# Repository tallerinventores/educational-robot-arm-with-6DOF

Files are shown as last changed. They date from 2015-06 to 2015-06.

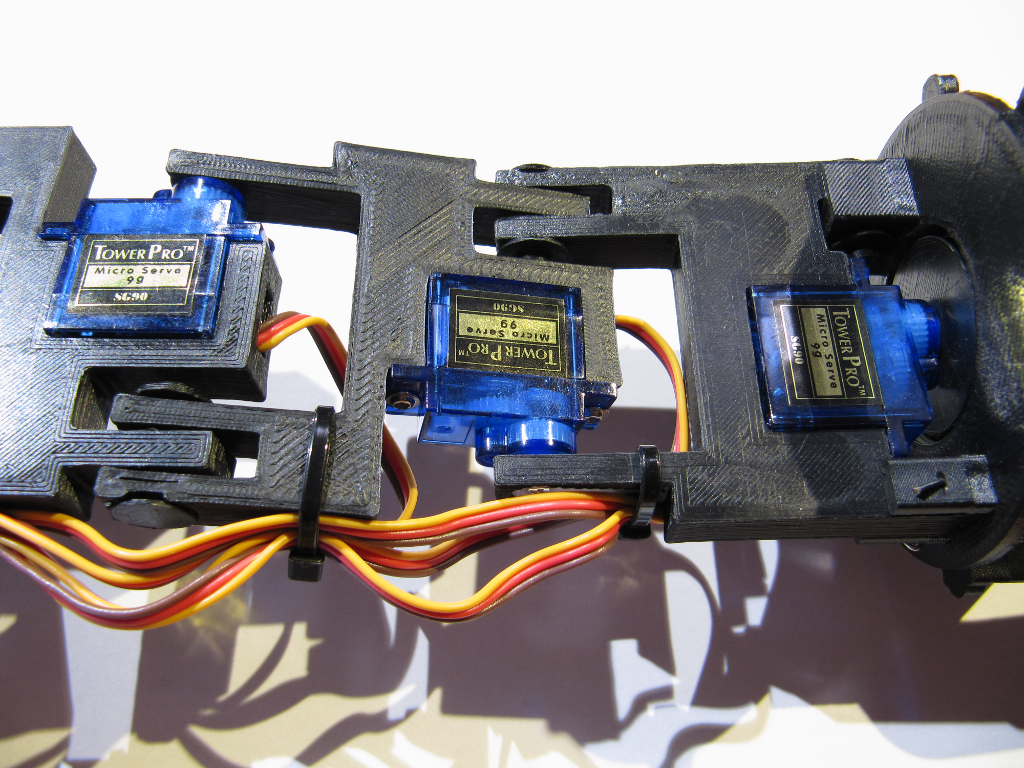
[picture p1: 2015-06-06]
img/photo-era6dof-4.png

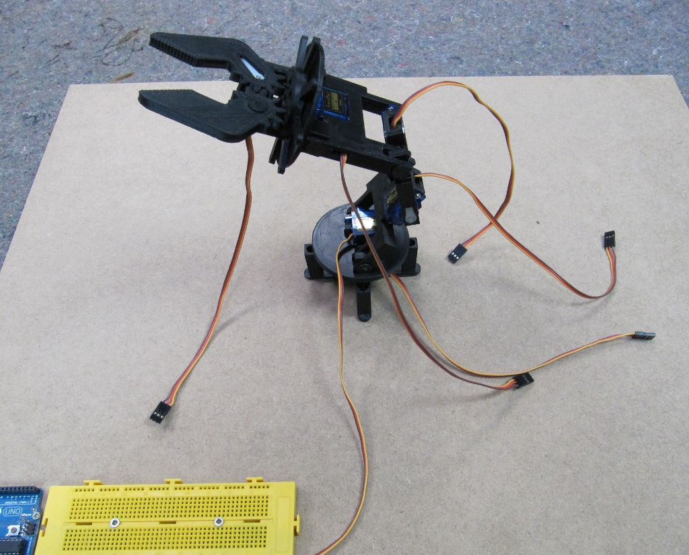
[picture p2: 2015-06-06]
img/photo-era6dof-1.png

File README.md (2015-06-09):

# Educational Robot Arm with 6DOF #

> Robot arm w/ 6DOF for educational use

* * *

## Resumen ##

Brazo robótico con seis grados de libertad para uso en entornos educativos. El
brazo ha sido desarrollado y optimizado para impresión 3D y pensando en su bajo
coste y facilidad de montaje y uso. Es personalizable al poder aumentar o
disminuir los grados de libertad, del mismo modo que permite controlarse desde
diferentes plataformas.

## Instalación ##

En esta sección se cubre la instalación de software y hardware para el montaje
recomendado, mediante [Scratch](https://scratch.mit.edu/) y
[Arduino](http://www.arduino.cc/).

### Requerimientos de software ###

Para poder usar Scratch (v2.0 online) con Arduino, es necesario
[s2a_fm](https://github.com/MrYsLab/s2a_fm) una extensión de Scratch para
comunicarse con Arduino. Para generar los archivos aptos para la impresora 3D
desde los archivos `.stl` será necesario adicionalmente un software para esta
función, como puede ser [Slic3r](http://slic3r.org/).

Ver los requerimientos de mencionados programas previamente.

### Requerimientos de hardware ###

Será necesario para su montaje y uso una fuente de alimentación que proporcione
7.5W a 5V, un Arduino Uno o equivalente, seis servomotores tipo 9g con sus
correspondientes accesorios (tornillos y cuernos). El brazo está optimizado para
usar los servos **TowerPro SG90**.

## Uso ##

Instrucciones de montaje y puesta en marcha.

### Montaje del brazo robótico ###

1.  Imprimir una unidad de los archivos `feet.stl`, `grip.stl`, `plate.stl`,
    `wrist`, `rest.stl`, `axle.stl`, `left_jaw.stl` and `right_jaw.stl`.
    Imprimir dos unidades de `arm.stl`. Imprimir cinco unidades de
    `fastener.stl` y `clip.stl`. Puede ser necesario repasar las piezas impresas
    con el fin de eliminar rebabas.  
2.  Presentar la base del brazo (_feet_) en un tablero y atornillarlo al mismo
    con cuatro tornillos para madera.  
3.  Colocar un servo (sin cuerno) en la base, haciéndo coincidir el eje del
    mismo con el centro de la base y atornillarlo a la misma con los tornillos
    de montaje del servo.  
4.  Poner el cuerno del servo sobre la huella con su forma en la parte inferior
    del plato (_grip_), considerando que el eje estará en hacia abajo.  
5.  Insertar el plato (_plate_) en la pieza anterior, asegurando que el cuerno
    encaja en su posición.  
6.  Comprobar que una vez colocado el conjunto del plato sobre el servo, éste
    realiza el giro de la forma deseada. En ese momento se puede atornillar el
    servo al cuerno con el tornillo provisto por el servo.  
7.  Fijar el siguiente servo con dos tornillos en la parte superior del plato,
    de forma que quede el eje centrado con respecto al plato.  
8.  Del primer tramo del brazo (_arm_), hacer coincidir el orificio destinado
    para el cuerno del servo en el eje del mismo mientras que se inserta el otro
    extremo en el saliente del plato.  
9.  Asegurar el brazo en esta posición usando un pasador (_fastener_ y _clip_),
    insertando el primero desde fuera hacia dentro, y retenerlo aquí con el
    segundo.  
10. Encastrar el cuerno en el brazo y asegurar que el servo es capaz de realizar
    giro completo de un extremo al otro. Entonces atornillarlo al servo.  
11. Atornillar un servo en el extremo del tramo del brazo recién montado, con el
    eje lo más distante a la base.  
12. Repetir los pasos ocho al once para el siguiente tramos de brazo (_arm_),
    estándo este montado rotado con respecto al anterior.   
13. De la misma manera, poner el último tramo (_wrist_) en la parte superior del
    brazo, también rotado con respecto al tramo intermedio.  
14. Introducir el servo del último tramo de forma que el eje del mismo quede
    centrado y atornillarlo.  
15. Hacer coincidir los dos orificios del último tramo montado con los
    respectivos del asiento (_rest_) y fijarlos. El grande mediante pasador como
    anteriormente y el pequeño con un alambre y doblándolo después. Un clip para
    papel es perfecto para esta función. Cortar el sobrante una vez doblado en
    los extremos.  
16. Encajar las dos piezas que permitirán que rote la pinza (_gripper_ y
    _axle_). Insertar el cuerno del servo en la endidura central de los mismos.  
17. Presentar este bloque contra el asiento y asegurar que gira de la forma
    deseada antes de atornillar el cuerno al servo.  
18. Montar el último servo en la parte más alta del brazo, con el eje hacia el
    centro. Atornillarlo por la parte externa.  
19. Con el cuerno del servo dentro de la mitad derecha de la pinza
    (_right\_jaw_), insertarlo en el eje del servo correspondiente y asegurar
    que realiza el giro necesario. Acto seguido atornillarlo.  
20. Colocar la otra mitad de pinza (_left\_jaw_), engranarla con la primera de
    forma que realicen el cierre en el centro. Fijarlo al cuerpo del brazo con
    un pasador.   
21. Realizar una correcta gestión de cableado para asegurar que todos llegan
    hasta la base sin impedir el movimiento de cada tramo, ni que son aplastado
    por los mismos. Puede ser necesario extender algunos de ellos.

### Conexión eléctrica ###

Todas las alimentaciones de los servomotores van en paralelo y a la fuente de
alimentación. Las señales de control de los servos van a Arduino, usando las
conexiones del dos al siete para los servos de la pinza a la base,
respectivamente y por orden. La masa del Arduino y de la fuente de alimentación
ha de ser compartida. Conectar el Arduino a un puerto USB libre del ordenador a
usar.

### Firmware ###

El Arduino deberá tener cargado el firmware Firmata (incluido con Arduino IDE
bajo en nombre de `StandardFirmata`).

### Software ###

Con el Arduino conectado al ordenador, lanzar s2a_fm con el nombre del puerto
donde realizar la comunicación con Arduino. Por ejemplo:

        python s2a_fm.py /dev/ttyACM0

Abrir Scratch y cargar el proyecto `educational-robot-arm-with-6DOF.sb2`, una
vez hecho, se podrá ver en la interfaz gráfica los posibles movimientos del
brazo en forma de flechas para dichas órdenes. Se presentan dos formas de mover
el brazo:

-   Semiautomática.  
-   Manual.

Para conmutar entre ellos se usa el botón situado en la esquina superior
derecha, que al ser pulsado mostrará las opciones **STEP**, **BIG STEP**,
**FULL** y **MANUAL**. Las tres primeras son semiautomáticas, mientras que la
última permite controlar el brazo robótico manualmente.

En semiautomático, es tan sencillo como pulsar la flecha correspondiente al
tramo y dirección deseado para realizar un movimiento angular de tantos grados
como esté seleccionado.

En manual, ha de seleccionarse el tramo a mover, después seleccionar el número
de grados a mover dicho tramo y deseleccionar el tramo para efectuar el
movimiento.

La interfaz gráfica incluye los límites físicos del brazo para prevenir la
rotación de los servos más allá de estos.

### Bugs ###

Se han observado los siguientes problemas:

-   Las dos partes de la pinza tienen cierta holgura, eso provoca que no se
    cierren alineadas.  
-   El brazo totalmente extendido en horizontal presenta demasiada carga para
    los servos más cercanos a la base.  
-   El software de control provoca al inicio movimientos extraños.  
-   En determinados momentos hay servos que se deshabilitan sin razón aparente.
    (Problema de PyMata?).  
-   Por protocolo de Firmata, es necesario un pequeño tiempo entre órdenes para
    asegurar que son recibidas y procesadas. (Implementado).

## Enlaces externos ##

Este proyecto también está presente en:

-   [Scratch](https://scratch.mit.edu/projects/65804696/).  
-   [Thingiverse](http://www.thingiverse.com/thing:436096).

## Créditos ##

Proyecto realizado por Taller de Inventores 2015, representado por:

-   kwendenarmo <kwendenarmo@akornsys-rdi.net>

Alumnos de Centro de Formación Padre Piquer:

-   G, Ayman El-  
-   S, Safaa

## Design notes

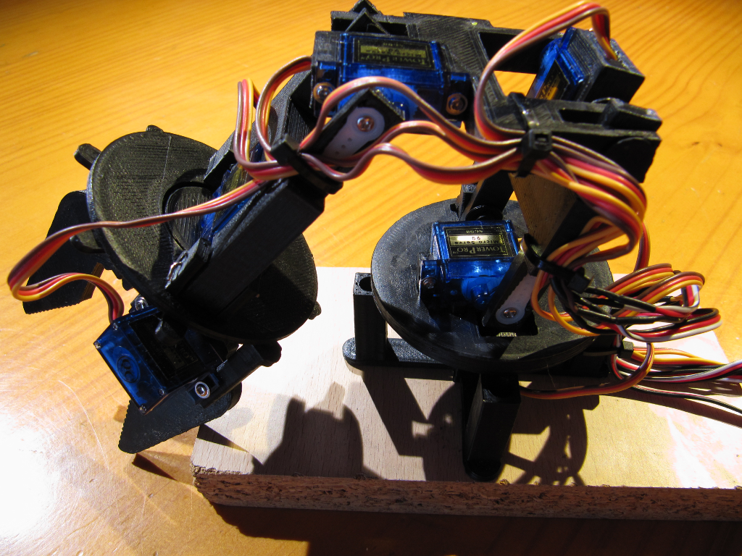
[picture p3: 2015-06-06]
img/photo-era6dof-2.png

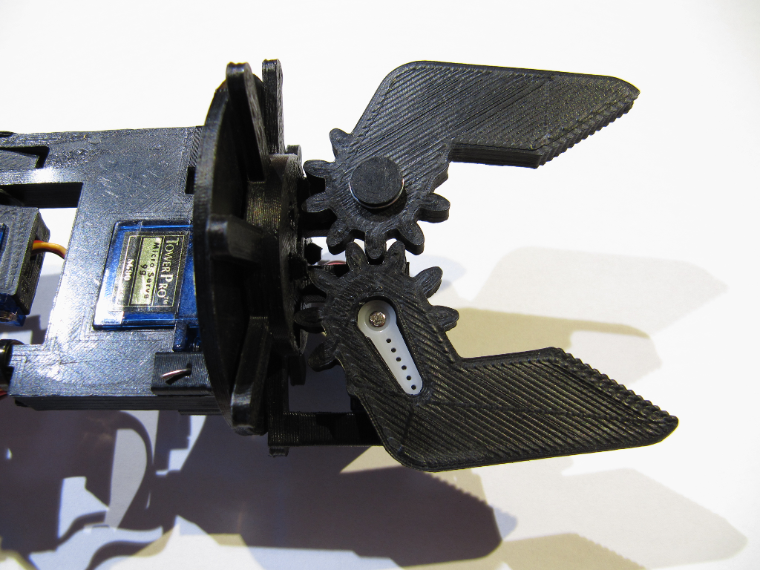
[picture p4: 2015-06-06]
img/photo-era6dof-5.png

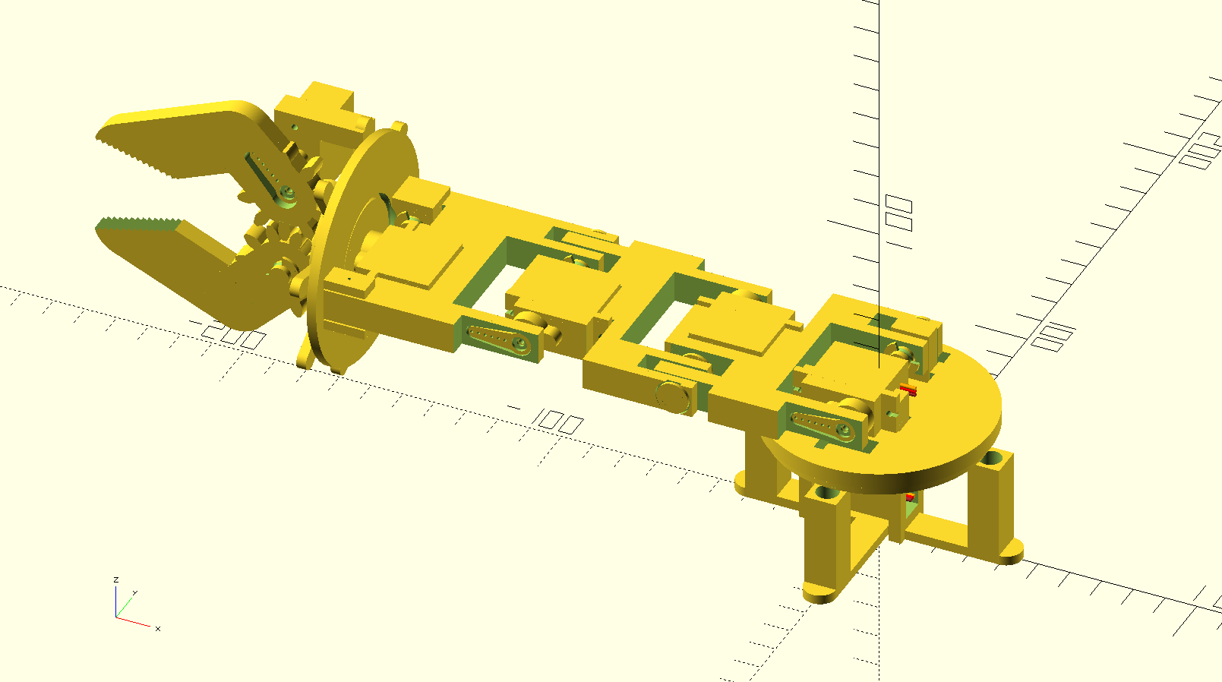
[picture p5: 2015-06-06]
img/render.png

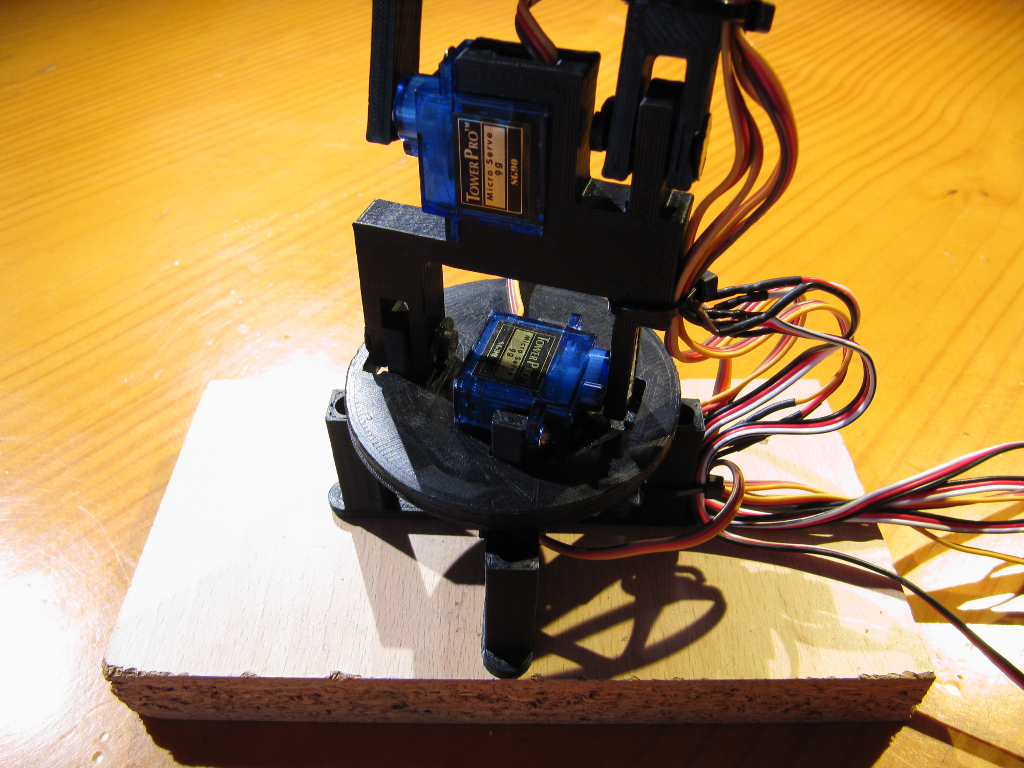
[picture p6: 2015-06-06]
img/photo-era6dof-3.png

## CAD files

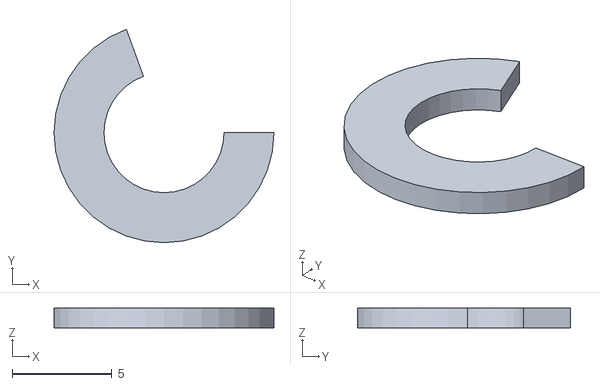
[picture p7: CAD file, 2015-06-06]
3d/clip.stl
11.0 x 10.7 x 1.00

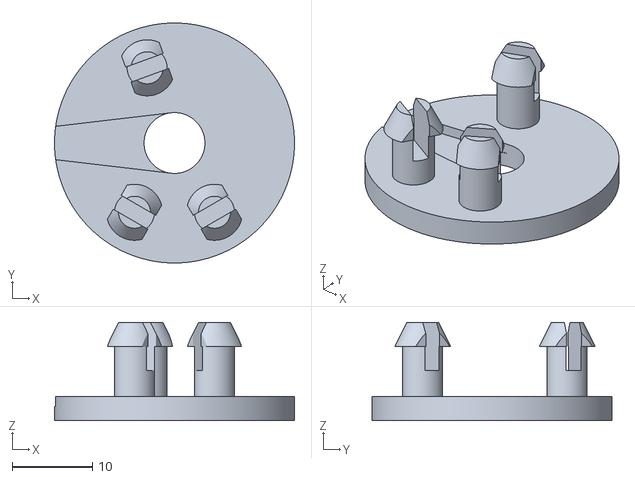
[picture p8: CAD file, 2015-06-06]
3d/axle.stl
30.0 x 30.0 x 12.2

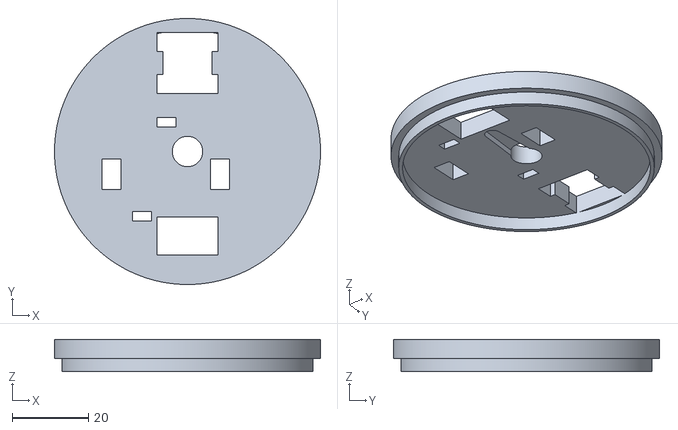
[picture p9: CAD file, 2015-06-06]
3d/plate.stl
70.0 x 70.0 x 8.50

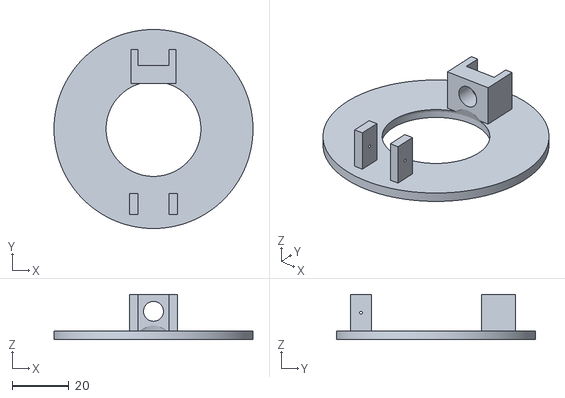
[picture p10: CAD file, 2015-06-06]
3d/rest.stl
70.0 x 70.0 x 16.0

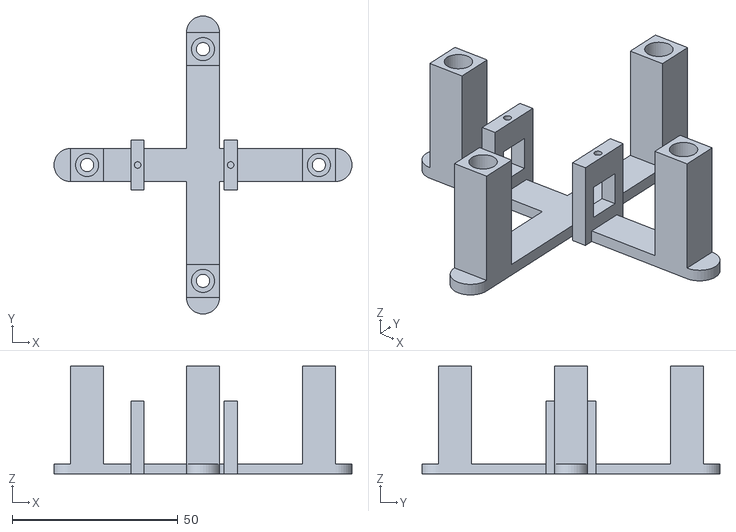
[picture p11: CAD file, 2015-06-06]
3d/feet.stl
90.0 x 90.0 x 32.5

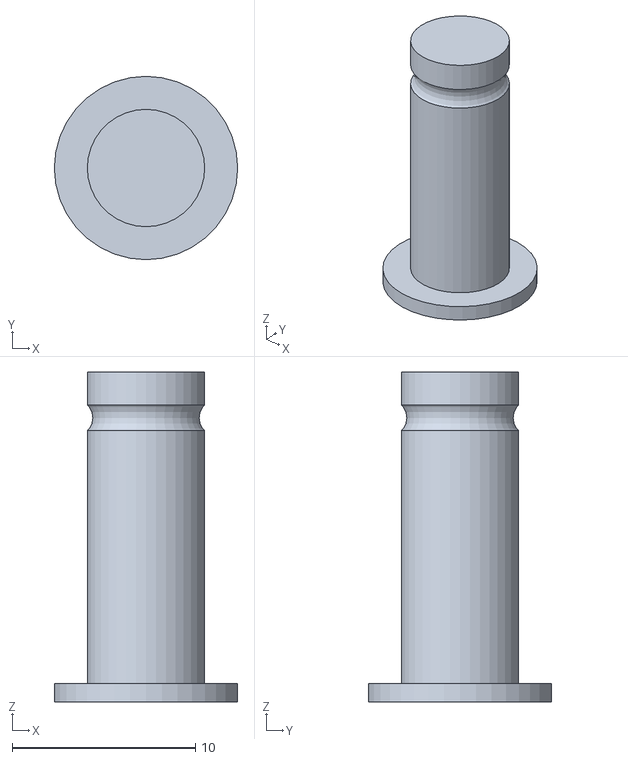
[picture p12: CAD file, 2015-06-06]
3d/fastener.stl
10.0 x 10.0 x 18.0

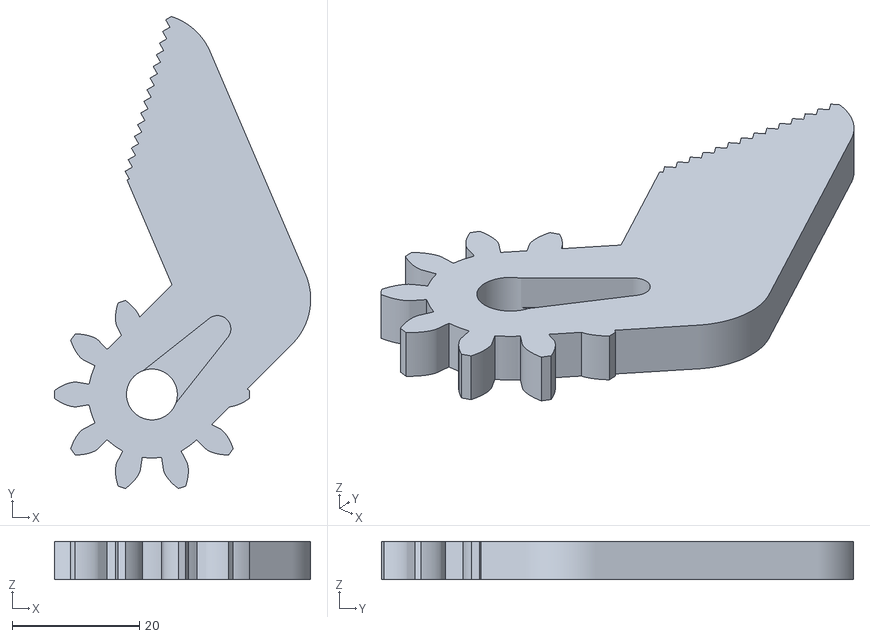
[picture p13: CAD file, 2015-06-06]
3d/right_jaw.stl
40.4 x 74.3 x 6.00

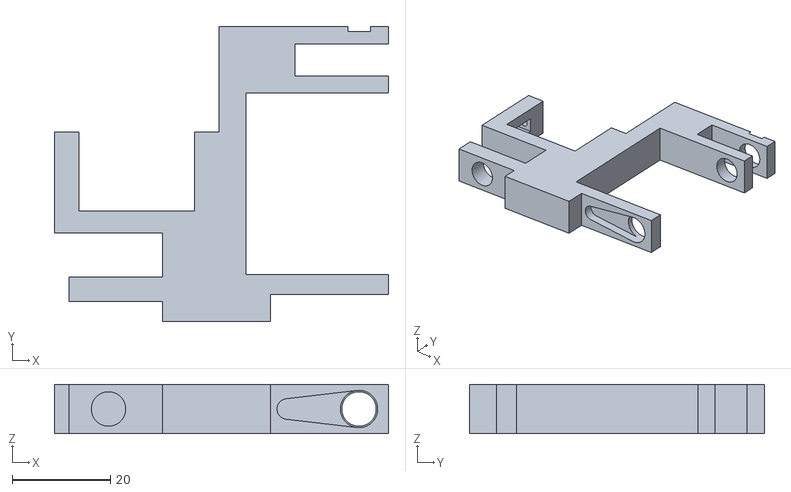
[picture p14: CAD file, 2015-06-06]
3d/arm.stl
68.0 x 60.0 x 10.0

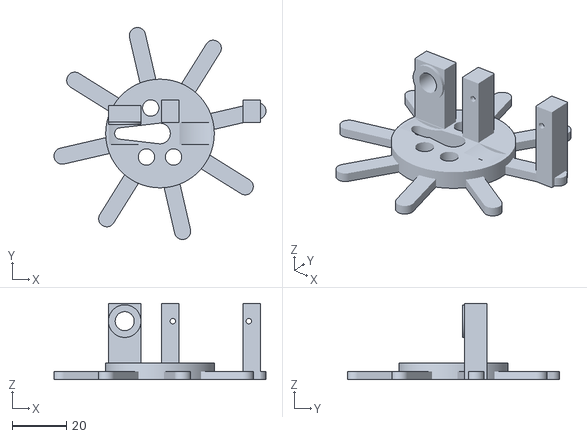
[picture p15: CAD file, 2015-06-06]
3d/gripper.stl
78.1 x 78.1 x 28.0

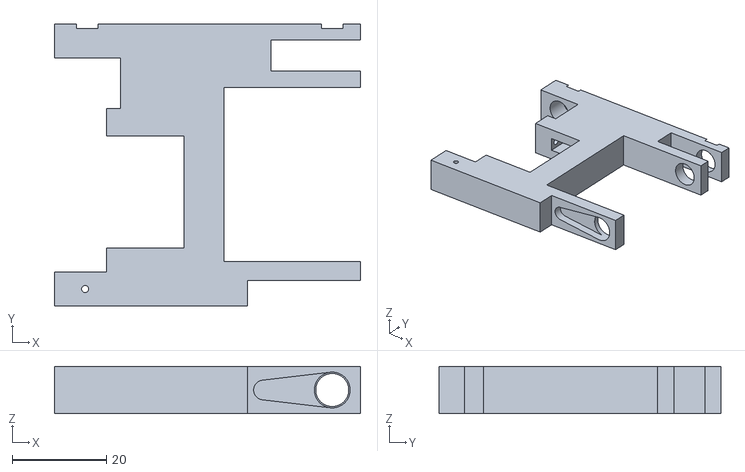
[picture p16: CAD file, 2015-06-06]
3d/wrist.stl
65.0 x 60.0 x 10.0

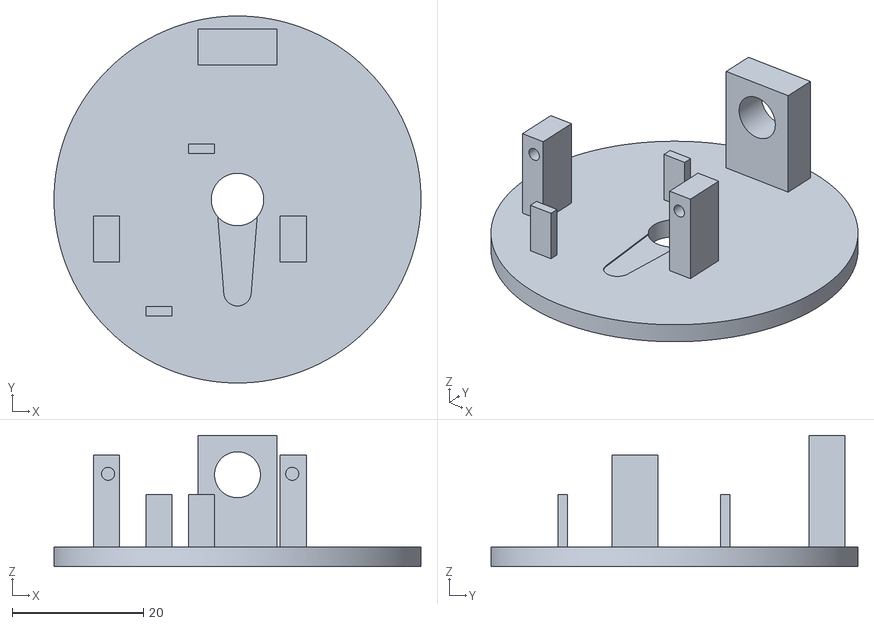
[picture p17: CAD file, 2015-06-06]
3d/grip.stl
56.0 x 56.0 x 20.0

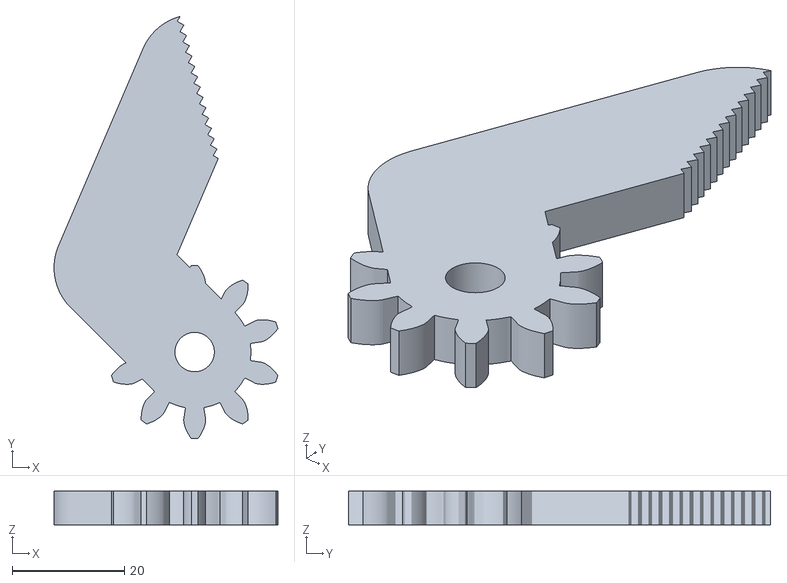
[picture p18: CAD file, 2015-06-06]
3d/left_jaw.stl
39.8 x 75.0 x 6.00

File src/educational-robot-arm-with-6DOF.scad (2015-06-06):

/* {{{ %%SECTION_HEADER%%
 * * * *
 * This header information is automatically generated by KodeUtils.
 *
 * File 'educational-robot-arm-with-6DOF.scad' edited by kwendenarmo,
 * last modified: 2015-04-06.
 * This file is part of 'educational-robot-arm-with-6DOF' package, please see
 * the readme files for more information about this file and this package.
 *
 * Copyright (C) 2014, 2015 by kwendenarmo <kwendenarmo@akornsys-rdi.net>
 * Released under the GNU GPLv3
 *
 *    This program is free software: you can redistribute it and/or modify
 *    it under the terms of the GNU General Public License as published by
 *    the Free Software Foundation, either version 3 of the License, or
 *    (at your option) any later version.
 *
 *    This program is distributed in the hope that it will be useful,
 *    but WITHOUT ANY WARRANTY; without even the implied warranty of
 *    MERCHANTABILITY or FITNESS FOR A PARTICULAR PURPOSE.  See the
 *    GNU General Public License for more details.
 *
 *    You should have received a copy of the GNU General Public License
 *    along with this program.  If not, see <http://www.gnu.org/licenses/>.
 *
 * * * *
 * %%EOS_HEADER%% }}}
 */

use <MCAD/involute_gears.scad>
$fn=360;

assemble = true;
debug = false;
showservos = true;

if (debug == true) {
    fastener();
}

if ((debug == false) && (assemble == true) ) {
    translate([-164,0,47]) rotate([0,-90,0]) gripper();
    translate([-161,-30,42]) wrist();
    translate([-110,30,52]) rotate([180,0,0]) arm();
    translate([-59,-30,42]) arm();
    translate([0,0,35.9]) plate();
    feet();
}

if ((debug == false) && (assemble == false) ) {
    gripper();
    //axle();
    //left_jaw();
    //right_jaw();
    //rest();
    //wrist();
    //arm();
    //fastener();
    //clip();
    //plate();
    //grip();
    //feet();
}

module gripper() {
    if (assemble == true) {
        translate([-13,11.5,22]) rotate([90,0,0]) fastener();
        translate([0,0,-2.5]) axle();
        translate([0,3,22]) union() {
            translate([13,0,0]) rotate([90,0,0]) right_jaw(); //close: rotate([90,345,0])
            translate([-13,0,0]) rotate([90,0,0]) left_jaw(); //close: rotate([90,15,0])
        }
    }
    translate([13,3.5,22]) rotate([-90,0,180]) servo9g(225); //close: servo9g(240)
    difference() {
        translate([0,0,0.5]) union() {
            for (i= [13:45:359]) {
                rotate([0,0,i]) hull() {
                    translate([37,0,0]) cylinder(r=3, h=3);
                    translate([-37,0,0]) cylinder(r=3, h=3);
                }
            }
            difference() {
                cylinder(r=20, h=6);
                union() {
                    translate([13,4,22]) rotate([90,0,0]) cylinder(r=17, h=8);
                    translate([-13,4,22]) rotate([90,0,0]) cylinder(r=17, h=8);
                }
            }
            translate([-19,4.25,0]) cube([12,6,28]);
            translate([-13,4.25,21.5]) rotate([90,0,0]) cylinder(r=6, h=1);
            translate([30.5,4,0]) cube([6.5,8.25,28]);
            translate([0.5,4,0]) cube([6.5,8.25,28]);
        }
        union() {
            translate([0,0,-3]) cylinder(r=4, h=12);
            translate([0,0,-1]) hull() {
                cylinder(r=3.8, h=10);
                translate([-14.6,0,0]) cylinder(r=2.1, h=10);
            }
            for (i= [110,300,240]) {
                rotate([0,0,i]) translate([10,0,0]) cylinder(r=3, h=10);
            }
            translate([-13,12,22]) rotate([90,0,0]) cylinder(r=3.5, h=10);
            translate([4.75,18,22]) rotate([90,0,0]) cylinder(r=1, h=17);
            translate([32.75,18,22]) rotate([90,0,0]) cylinder(r=1, h=17);
            translate([4.75,18,22]) rotate([90,0,0]) cylinder(r=3, h=4);
            translate([32.75,18,22]) rotate([90,0,0]) cylinder(r=3, h=4);
        }
    }
}

module axle() {
    difference() {
        union() {
            cylinder(r=15, h=3);
            for (i= [110,300,240]) {
                rotate([0,0,i]) translate([10,0,0]) difference() {
                    union() {
                        cylinder(r=2.5, h=9.25);
                        translate([0,0,9.25]) cylinder(r1=3.5, r2=2, h=3);
                    }
                    union() {
                        translate([-5,2.5,9]) cube([10,4,4]);
                        translate([-5,-6.5,9]) cube([10,4,4]);
                        translate([-1,-5,6.25]) cube([2,10,7]);
                    }
                }
            }
        }
        union() {
            translate([0,0,-1]) cylinder(r=4, h=5);
            translate([0,0,1.75]) hull() {
                cylinder(r=3.8, h=3);
                translate([-14.6,0,0]) cylinder(r=2.1, h=3);
            }
        }
    }
}

module jaw(angle) {
    difference() {
        union() {
            translate([0,0,6]) rotate([180,0,angle]) gear(number_of_teeth=10, diametral_pitch=0.39, pressure_angle=20, clearance = 0.2, gear_thickness=6, rim_thickness=6, rim_width=6, hub_thickness=6, hub_diameter=20, bore_diameter=4, circles=0, backlash=0.5, twist=0, involute_facets=0, flat=false);
            hull() {
                translate([0,50,0]) cylinder(r=10, h=6);
                translate([15,15,0]) cylinder(r=10, h=6);
            }
            hull() {
                cylinder(r=10, h=6);
                translate([15,15,0]) cylinder(r=10, h=6);
            }
        }
        union() {
            translate([-4.5,35,-1]) rotate([0,0,-15]) scale([-1,1,1]) cube([20,40,8]);
            if (angle != 0) {
                translate([-4.75,35,0]) for(i = [-3:1.9:30]) {
                    translate([i*sin(15),i*cos(15),-1]) rotate([0,0,30]) cube([2,2,8]);
                }
            }
            else {
                translate([-4.75,35,0]) for(i = [-4:1.9:30]) {
                    translate([i*sin(15),i*cos(15),-1]) rotate([0,0,30]) cube([2,2,8]);
                }
            }
        }
    }
}

module right_jaw() {
    difference() {
        jaw(0);
        union() {
            translate([0,0,-1])cylinder(r=4, h=8);
            translate([0,0,2]) rotate([0,0,-45]) hull() {
                cylinder(r=3.8, h=5);
                translate([0,14.6,0]) cylinder(r=2.1, h=5);
            }
        }
    }
}

module left_jaw() {
    mirror() difference() {
        jaw(18);
        union() {
            translate([0,0,-1])cylinder(r=3.5, h=8);
        }
    }
}

module rest() {
    difference() {
        union() {
                cylinder(r=35, h=3);
                translate([-8,16,0]) cube([16,6.25,16]);
                translate([-8,16,0]) cube([2.5,12,16]);
                translate([5.5,16,0]) cube([2.5,12,16]);
                translate([-8.5,-30,0]) cube([3,7.25,16]);
                translate([5.5,-30,0]) cube([3,7.25,16]);
        }
        union() {
                translate([0,15,10]) rotate([-90,0,0]) cylinder(r=3.5, h=9);
                translate([9,-26.375,9.5]) rotate([0,-90,0]) cylinder(r=0.5, h=18);
                translate([0,0,-1]) cylinder(r=17, h=3.1);
                translate([0,0,2]) cylinder(r1=17, r2=16, h=3);
        }
    }
}

module wrist() {
    if (assemble == true) {
        translate([59,60.5,5]) rotate([90,0,0]) fastener();
        translate([7,60.5,5]) rotate([90,0,0]) fastener();
        translate([-3,30,5]) rotate([0,90,0]) rest();
    }
    translate([0,30,5]) rotate([-90,0,90]) servo9g(90);
    difference() {
        union() {
            cube([65,60,10]);
        }
        union() {
            translate([59,-1,5]) rotate([-90,0,0]) cylinder(r=3.5, h=62); //falso eje delantero
            translate([59,59,5]) rotate([-90,0,0]) cylinder(r=5.5, h=2); //rebaje fastener delantero
            translate([7,50,5]) rotate([-90,0,0]) cylinder(r=3.5, h=15); //falso eje trasero
            translate([7,59,5]) rotate([-90,0,0]) cylinder(r=5.5, h=2); //rebaje fastener trasero
            translate([36,9.5,-1]) cube([30,37,12]); //hueco servo plate
            translate([46,50,-1]) cube([20,6.5,12]); //hueco anclaje fastener
            translate([41,-1,-1]) cube([25,6.5,12]); //hueco anclaje horn servo
            translate([59,10,5]) rotate([90,90,0]) cylinder(r=3.8, h=5);
            translate([59,8,5]) rotate([90,90,0]) hull() { //horn
                cylinder(r=3.8, h=2.6);
                translate([0,-14.6,0]) cylinder(r=2.1, h=2.6);
            }
            translate([-1,7.25,-1]) cube([12,45.5,12]);
            translate([10.5,12.4,-1]) cube([17,23.75,12]);
            translate([10,10.25,5]) rotate([0,90,0]) cylinder(r=1, h=7);
            translate([10,38.375,5]) rotate([0,90,0]) cylinder(r=1, h=7);
            translate([17,31,3]) cube([10,30,4]);
            translate([10,42,-1]) cube([4,10.75,12]);
            translate([6.5,3.65,-4]) cylinder(r=0.75, h=18);
        }
    }
}
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
